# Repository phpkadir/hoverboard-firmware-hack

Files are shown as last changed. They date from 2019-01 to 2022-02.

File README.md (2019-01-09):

# Hoverboard-Firmware-Hack



### Under heavy development

This firmware is much better than the old one. tested up to 40A / 60V, no dead board so far :)
But The Firmware can't do inpossible Stuff pleace stay at 12s (under 50V) because the boards use condensators up to 50V higher voltages damage them.

This repo contains open source firmware for generic Hoverboard Mainboards.
The firmware you can find here allows you to use your Hoverboard Hardware (like the Mainboard, Motors and Battery) for cool projects like driving armchairs, person-tracking transportation robots and every other application you can imagine that requires controlling the Motors.

If you want an overview of what you can do with this firmware, here is a ~40min video of a talk about this project:
https://media.ccc.de/v/gpn18-95-howto-moving-objects

---

#### Hardware
otter

The original Hardware supports two 4-pin cables that originally were connected to the two sensor boards. They break out GND, 12/15V and USART2&3 of the Hoverboard mainboard.
Both USART2 & 3 can be used for UART and I2C, PA2&3 can be used as 12bit ADCs.

The reverse-engineered schematics of the mainboard can be found here:
http://vocke.tv/lib/exe/fetch.php?media=20150722_hoverboard_sch.pdf

---

#### Flashing
To build the firmware, just type "make". Make sure you have specified your gcc-arm-none-eabi binary location in the Makefile ("PREFIX = ..."). Right to the STM32, there is a debugging header with GND, 3V3, SWDIO and SWCLK. Connect GND, SWDIO and SWCLK to your SWD programmer, like the ST-Link found on many STM devboards.

Make sure you hold the powerbutton or connect a jumper to the power button pins while flashing the firmware, as the STM might release the power latch and switches itself off during flashing. Battery > 36V have to be connected while flashing.

To flash the STM32, use the ST-Flash utility (https://github.com/texane/stlink).

If you never flashed your mainboard before, the STM is probably locked. To unlock the flash, use the following OpenOCD command:

```
make unlock
```
if it fails use
```
make fallback_unlock
```
if it doest work now use *Windows utility*

Then you can simply flash the firmware:
```
make flash
```

---
#### Troubleshooting
First, check that power is connected and voltage is >36V while flashing.
If the board draws more than 100mA in idle, it's probably broken.

If the motors do something, but don't rotate smooth and quietly, try to use an alternative phase mapping. Usually, color-correct mapping (blue to blue, green to green, yellow to yellow) works fine. However, some hoverboards have a different layout then others, and this might be the reason your motor isn't spinning.

Nunchuck not working: Use the right one of the 2 types of nunchucks. Use i2c pullups.

Nunchuck or PPM working bad: The i2c bus and PPM signal are very sensitive to emv distortions of the motor controller. They get stronger the faster you are. Keep cables short, use shielded cable, use ferrits, stabalize voltage in nunchuck or reviever, add i2c pullups. To many errors leads to very high accelerations which triggers the protection board within the battery to shut everything down.

Most robust way for input is to use the ADC and potis. It works well even on 1m unshielded cable. Solder ~100k Ohm resistors between ADC-inputs and gnd directly on the mainboard. Use potis as pullups to 3.3V.

---

#### Examples

We want support many projects like a longboard. our firmware will support variable sync with i2c and an i2c display PPM-Sum signal and ADC input
It will get new fieldweakoning algorythm and a timing algorythm

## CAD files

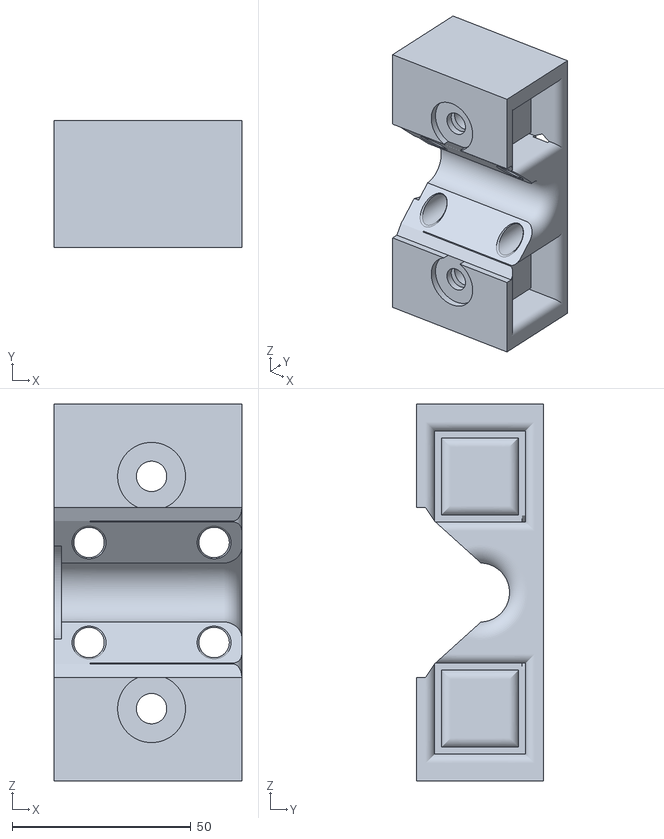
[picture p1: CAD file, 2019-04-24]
3d printable files/bobbycar/hinterachse1.stl
52.5 x 35.5 x 105.5

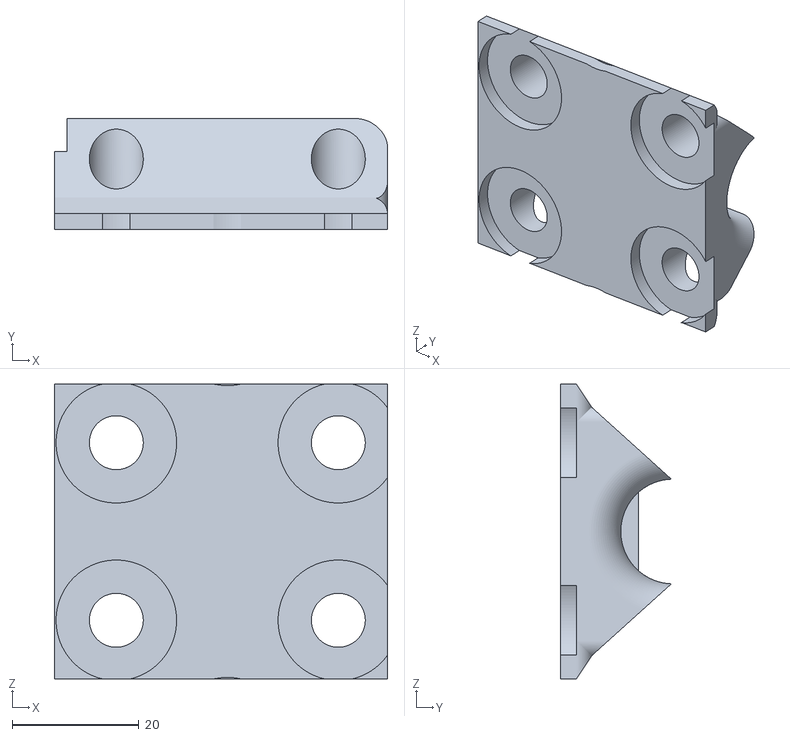
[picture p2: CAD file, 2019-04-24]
3d printable files/bobbycar/hinterachse2.stl
52.5 x 17.5 x 46.5

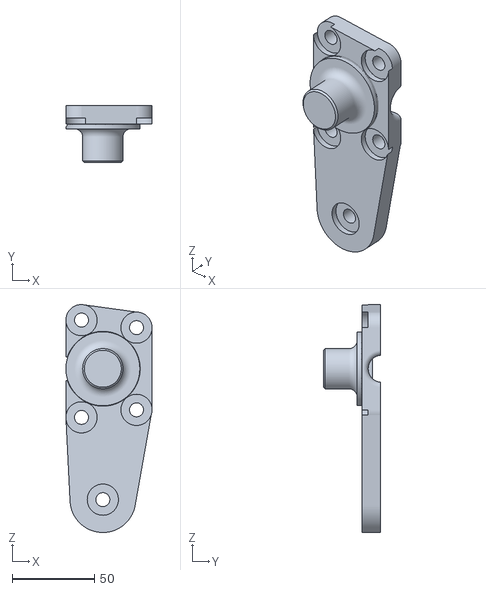
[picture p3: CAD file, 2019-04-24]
3d printable files/bobbycar/radaufnahme1 (1x normal, 1x gespiegelt).stl
52.5 x 34.8 x 138.8

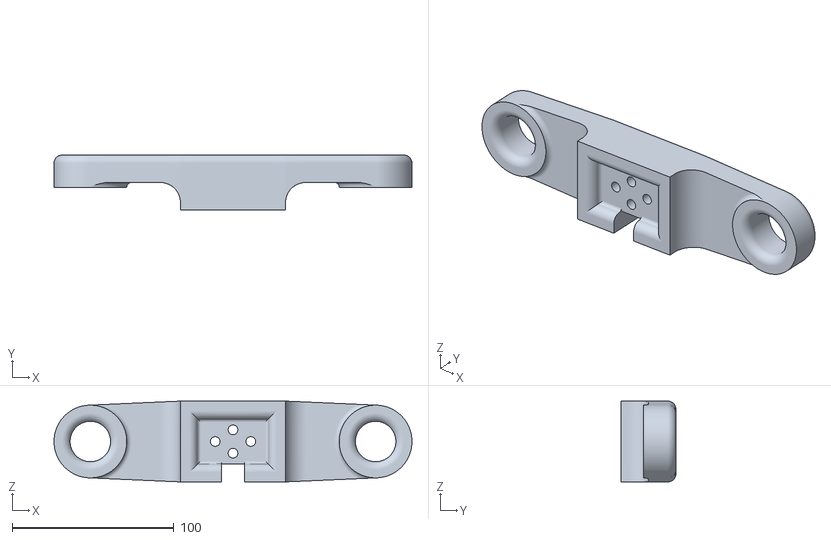
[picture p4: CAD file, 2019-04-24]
3d printable files/bobbycar/achsschenkel.stl
221.5 x 34.0 x 50.0

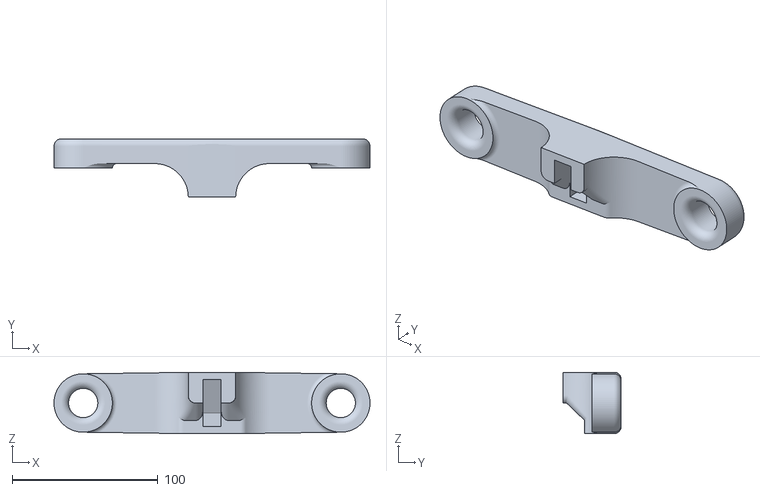
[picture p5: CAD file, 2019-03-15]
3d printable files/bobbycar/spurstange.stl
216.5 x 40.0 x 42.0

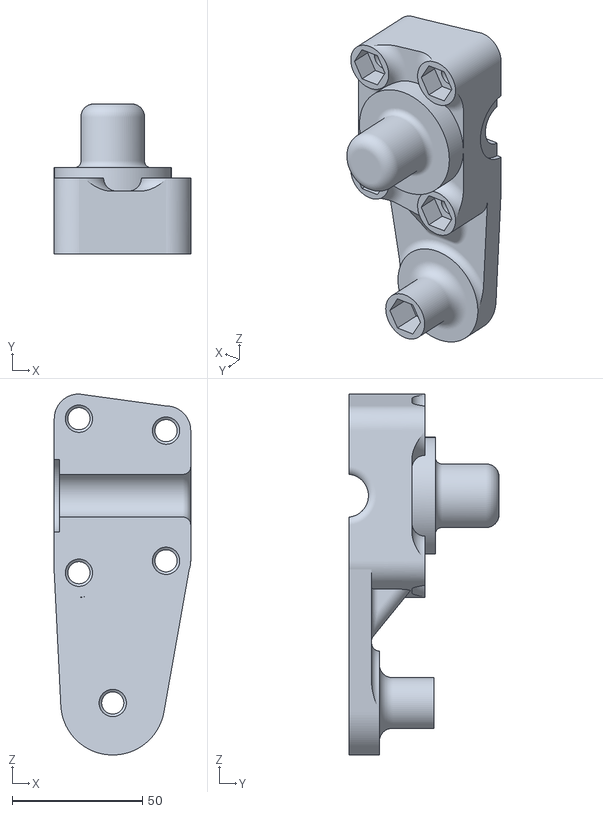
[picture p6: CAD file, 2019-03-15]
3d printable files/bobbycar/radaufnahme2 (1x normal, 1x gespiegelt).stl
52.5 x 57.8 x 138.8

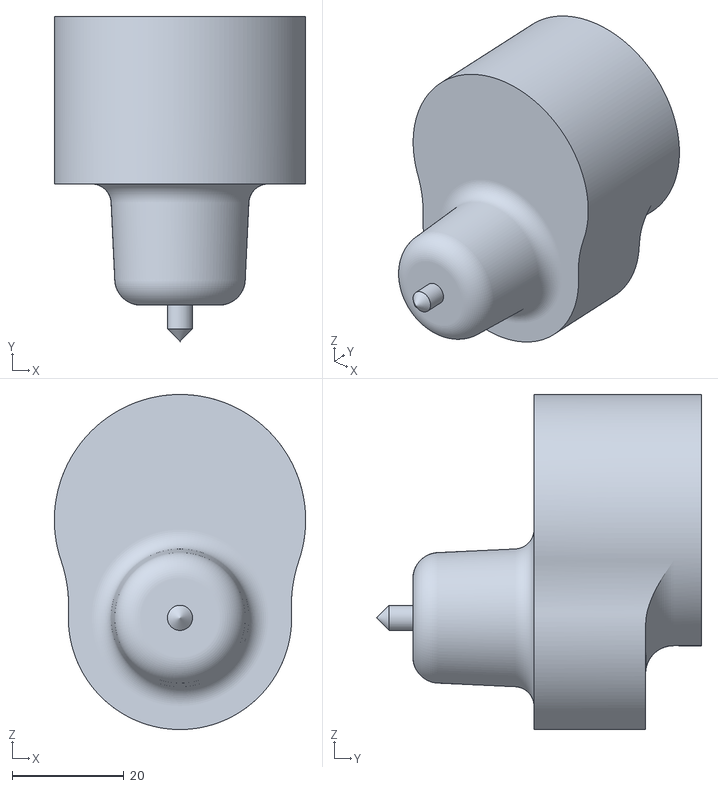
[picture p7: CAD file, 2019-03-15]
3d printable files/bobbycar/domlager (2x).stl
45.0 x 58.2 x 60.0

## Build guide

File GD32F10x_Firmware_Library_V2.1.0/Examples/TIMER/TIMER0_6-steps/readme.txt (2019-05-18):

/*!
    \file  readme.txt
    \brief description of the TIMER0 6-steps demo

    \version 2014-12-26, V1.0.0, firmware for GD32F10x
    \version 2017-06-20, V2.0.0, firmware for GD32F10x
    \version 2018-07-31, V2.1.0, firmware for GD32F10x
*/

/*
    Copyright (c) 2018, GigaDevice Semiconductor Inc.

    All rights reserved.

    Redistribution and use in source and binary forms, with or without modification, 
are permitted provided that the following conditions are met:

    1. Redistributions of source code must retain the above copyright notice, this 
       list of conditions and the following disclaimer.
    2. Redistributions in binary form must reproduce the above copyright notice, 
       this list of conditions and the following disclaimer in the documentation 
       and/or other materials provided with the distribution.
    3. Neither the name of the copyright holder nor the names of its contributors 
       may be used to endorse or promote products derived from this software without 
       specific prior written permission.

    THIS SOFTWARE IS PROVIDED BY THE COPYRIGHT HOLDERS AND CONTRIBUTORS "AS IS" 
AND ANY EXPRESS OR IMPLIED WARRANTIES, INCLUDING, BUT NOT LIMITED TO, THE IMPLIED 
WARRANTIES OF MERCHANTABILITY AND FITNESS FOR A PARTICULAR PURPOSE ARE DISCLAIMED. 
IN NO EVENT SHALL THE COPYRIGHT HOLDER OR CONTRIBUTORS BE LIABLE FOR ANY DIRECT, 
INDIRECT, INCIDENTAL, SPECIAL, EXEMPLARY, OR CONSEQUENTIAL DAMAGES (INCLUDING, BUT 
NOT LIMITED TO, PROCUREMENT OF SUBSTITUTE GOODS OR SERVICES; LOSS OF USE, DATA, OR 
PROFITS; OR BUSINESS INTERRUPTION) HOWEVER CAUSED AND ON ANY THEORY OF LIABILITY, 
WHETHER IN CONTRACT, STRICT LIABILITY, OR TORT (INCLUDING NEGLIGENCE OR OTHERWISE) 
ARISING IN ANY WAY OUT OF THE USE OF THIS SOFTWARE, EVEN IF ADVISED OF THE POSSIBILITY 
OF SUCH DAMAGE.
*/

  This demo is based on the GD32107C-EVAL board, it shows how to 
configure the TIMER0 peripheral to generate three complementary TIMER0 signals 
(for BLDC ) with dead time.

  TIMER0CLK is fixed to systemcoreclock, the TIMER0 prescaler is equal to 108 so the 
TIMER0 counter clock used is 1MHz.
  
  Channel change sequence: 
  AB`->AC`->BC`->BA`->CA`->CB`
step1:1-0  0-1  0-0   (CH0-CH0N  CH1-CH1N  CH2-CH2N)
step2:1-0  0-0  0-1   (CH0-CH0N  CH1-CH1N  CH2-CH2N)
step3:0-0  1-0  0-1   (CH0-CH0N  CH1-CH1N  CH2-CH2N)
step4:0-1  1-0  0-0   (CH0-CH0N  CH1-CH1N  CH2-CH2N)
step5:0-1  0-0  1-0   (CH0-CH0N  CH1-CH1N  CH2-CH2N)
step6:0-0  0-1  1-0   (CH0-CH0N  CH1-CH1N  CH2-CH2N)

  Connect the TIMER0 pins to a logic analyzer to monitor the different waveforms:
  - TIMER0_CH0  pin (PA8)
  - TIMER0_CH0N pin (PB13)
  - TIMER0_CH1  pin (PA9)
  - TIMER0_CH1N pin (PB14)
  - TIMER0_CH2  pin (PA10)
  - TIMER0_CH2N pin (PB15)

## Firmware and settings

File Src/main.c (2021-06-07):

/*
* This file is part of the hoverboard-firmware-hack project.
*
* Copyright (C) 2017-2018 Rene Hopf <renehopf@mac.com>
* Copyright (C) 2017-2018 Nico Stute <crinq@crinq.de>
* Copyright (C) 2017-2018 Niklas Fauth <niklas.fauth@kit.fail>
*
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
* You should have received a copy of the GNU General Public License
* along with this program.  If not, see <http://www.gnu.org/licenses/>.
*/

#include <stdbool.h>
#include <stdint.h>
#include "stm32f1xx_hal.h"  // main code for stm32 controller
#include "defines.h"  // for the macros
#include "setup.h"  // for access the functions form setup
#include "bldc.h"  // for the main control variables
#include "buzzertones.h"
#include "hd44780.h"  // for the display
#include "config.h"  // the config
#include "comms.h"
#include "control.h"
#include "generic_device.h"
void SystemClock_Config(void);

void init(){
    HAL_Init();
    __HAL_RCC_AFIO_CLK_ENABLE();
    HAL_NVIC_SetPriorityGrouping(NVIC_PRIORITYGROUP_4);
    /* System interrupt init*/
    /* MemoryManagement_IRQn interrupt configuration */
    HAL_NVIC_SetPriority(MemoryManagement_IRQn, 0, 0);
    /* BusFault_IRQn interrupt configuration */
    HAL_NVIC_SetPriority(BusFault_IRQn, 0, 0);
    /* UsageFault_IRQn interrupt configuration */
    HAL_NVIC_SetPriority(UsageFault_IRQn, 0, 0);
    /* SVCall_IRQn interrupt configuration */
    HAL_NVIC_SetPriority(SVCall_IRQn, 0, 0);
    /* DebugMonitor_IRQn interrupt configuration */
    HAL_NVIC_SetPriority(DebugMonitor_IRQn, 0, 0);
    /* PendSV_IRQn interrupt configuration */
    HAL_NVIC_SetPriority(PendSV_IRQn, 0, 0);
    /* SysTick_IRQn interrupt configuration */
    HAL_NVIC_SetPriority(SysTick_IRQn, 0, 0);

    SystemClock_Config();

    __HAL_RCC_DMA1_CLK_DISABLE();
    MX_GPIO_Init();
    MX_TIM_Init();
    MX_ADC1_Init();
    MX_ADC2_Init();

    HAL_GPIO_WritePin(OFF_PORT, OFF_PIN, 1);  // set latch to on

    HAL_ADC_Start(&hadc1);
    HAL_ADC_Start(&hadc2);

    set_buzzer(startUpSound);

    HAL_GPIO_WritePin(LED_PORT, LED_PIN, 1);  // turn LED on for looking if the µC is working

    #ifdef CONTROL_PPM
      PPM_Init();
    #endif

      I2C_Init();
      HAL_Delay(50);

    load_eeprom();  // initialize variables from eeprom or initialize them
    while(HAL_GPIO_ReadPin(BUTTON_PORT, BUTTON_PIN));  // wait for button release
}

int main(void) {
restart = true;
main_start:  // only for defect boards if you think your hardware is working please remove
  init();
  device_init();
  set_bldc_motors(true);
  while(1) {
    HAL_Delay(3);
    device_specific();
    //START FINAL CODE
    if (HAL_GPIO_ReadPin(BUTTON_PORT, BUTTON_PIN)) {  // turnoff mechanism
      bool btn_release = false;
      unsigned long startTime = get_mainCounter();
      set_bldc_motors(false);
      while(get_mainCounter() < (startTime + (PWM_FREQ * 2))){  // check button for 2s for release to only turn off if its pressed for 2 secs
        if(!HAL_GPIO_ReadPin(BUTTON_PORT, BUTTON_PIN)){  // if button released
          btn_release = true;
          break;
        }
      }
      if(btn_release){
        set_buzzer(buttonRelease);
        set_bldc_motors(true);
        // do something
        device_button();
      }
      else{
        set_buzzer(shutDownSound);
        while (get_mainCounter() < (startTime + (PWM_FREQ * 10))) {
          if(!HAL_GPIO_ReadPin(BUTTON_PORT, BUTTON_PIN)){
            btn_release = true;
            break;
          }
        }  // wait for button release to turn off
        if(btn_release) {
          turnOff();
          break;
        } else {
          set_buzzer(resetSound);
          while(HAL_GPIO_ReadPin(BUTTON_PORT, BUTTON_PIN));
          turnOffWithReset();
          break;
        }
      }
    }
    //END FINAL CODE
    if(BATTERY_VOLTAGE2ADC12(DEBUG_VOLTAGE_LOW) < battery_voltage && battery_voltage < BATTERY_VOLTAGE2ADC12(DEBUG_VOLTAGE_HIGH)){
      // Debug mode
    }    
    else if (battery_voltage < lowBattery[0]) {
      set_buzzer(lowBatTones[0]);
      set_bldc_motors(false);
      HAL_Delay(200);
      turnOff();
      break;
    }
    for(uint8_t x=1;x<lowBattery_length;x++)
      if  (battery_voltage < lowBattery[x]) {
        set_buzzer(lowBatTones[x]);
        LIMIT_CURRENT(5 + 5*x);  // limiting the motorcurrent to a lower value
        break;
      }
  }
  goto main_start;  // if this goto is used the board is defect and everybody knows: "Defect boards are liking defect code" :D
}

/** System Clock Configuration
*/
void SystemClock_Config(void) {
  RCC_OscInitTypeDef RCC_OscInitStruct;
  RCC_ClkInitTypeDef RCC_ClkInitStruct;
  RCC_PeriphCLKInitTypeDef PeriphClkInit;

  /**Initializes the CPU, AHB and APB busses clocks
    */
  RCC_OscInitStruct.OscillatorType      = RCC_OSCILLATORTYPE_HSI;
  RCC_OscInitStruct.HSIState            = RCC_HSI_ON;
  RCC_OscInitStruct.HSICalibrationValue = 16;
  RCC_OscInitStruct.PLL.PLLState        = RCC_PLL_ON;
  RCC_OscInitStruct.PLL.PLLSource       = RCC_PLLSOURCE_HSI_DIV2;
  RCC_OscInitStruct.PLL.PLLMUL          = RCC_PLL_MUL16;
  HAL_RCC_OscConfig(&RCC_OscInitStruct);

  /**Initializes the CPU, AHB and APB busses clocks
    */
  RCC_ClkInitStruct.ClockType      = RCC_CLOCKTYPE_HCLK | RCC_CLOCKTYPE_SYSCLK | RCC_CLOCKTYPE_PCLK1 | RCC_CLOCKTYPE_PCLK2;
  RCC_ClkInitStruct.SYSCLKSource   = RCC_SYSCLKSOURCE_PLLCLK;
  RCC_ClkInitStruct.AHBCLKDivider  = RCC_SYSCLK_DIV1;
  RCC_ClkInitStruct.APB1CLKDivider = RCC_HCLK_DIV2;
  RCC_ClkInitStruct.APB2CLKDivider = RCC_HCLK_DIV1;

  HAL_RCC_ClockConfig(&RCC_ClkInitStruct, FLASH_LATENCY_2);

  PeriphClkInit.PeriphClockSelection = RCC_PERIPHCLK_ADC;
  PeriphClkInit.AdcClockSelection    = RCC_ADCPCLK2_DIV8;
  HAL_RCCEx_PeriphCLKConfig(&PeriphClkInit);

  /**Configure the Systick interrupt time
    */
  HAL_SYSTICK_Config(HAL_RCC_GetHCLKFreq() / 1000);

  /**Configure the Systick
    */
  HAL_SYSTICK_CLKSourceConfig(SYSTICK_CLKSOURCE_HCLK);

  /* SysTick_IRQn interrupt configuration */
  HAL_NVIC_SetPriority(SysTick_IRQn, 0, 0);
}

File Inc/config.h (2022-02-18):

#pragma once
#include "stm32f1xx_hal.h"

// ################################################################################

#define PWM_FREQ         16000      // PWM frequency in Hz default 16k  // h bridge pwm frequency: OC -> lovering deadtime!
#define DEAD_TIME        32         // PWM deadtime        default 32 0.5µS   // h bridge calibration for mosfet burning them OC possible
#define BAT_CALIB_REAL_VOLTAGE        43.0       // input voltage measured by multimeter
#define BAT_CALIB_ADC                 1704       // adc-value measured by mainboard (value nr 5 on UART debug output)

//device specific
#define DEAD_ZONE 64
#define BAT_CELL_CNT     10.0
#define BAT_FULL_CELL    4.2
#define BAT_RATED_CELL   3.6
#define BAT_LOW1_CELL    3.4
#define BAT_LOW2_CELL    3.2
#define BAT_LOW_DEAD_CELL 3.0
#define DEBUG_VOLTAGE_LOW 33.5
#define DEBUG_VOLTAGE_HIGH 36.5
#define THROTTLE_REVERSE_MAX (-(THROTTLE_MAX * 3 / 10))
//#define THROTTLE_REVERSE_MAX (-THROTTLE_MAX)
#define BEEPS_BACKWARD

#define I2C_MASTER
// ################################################################################

//#define DEBUG_SERIAL_USART3         // left sensor board cable, disable if ADC or PPM is used!
//#define DEBUG_SERIAL_USART3         // right sensor board cable, disable if I2C (nunchuck) is used!
//#define DEBUG_BAUD       115200     // UART baud rate
//#define DEBUG_SERIAL_SERVOTERM
//#define DEBUG_SERIAL_ASCII          // human readable output. i.e. "345;1337;0;0\n\r"

//#define CONTROL_SERIAL_USART2
//#define CONTROL_BAUD       19200     // control via usart from eg an Arduino or raspberry
// for Arduino, use void loop(void){ Serial.write((uint8_t *) &steer, sizeof(steer)); Serial.write((uint8_t *) &speed, sizeof(speed));delay(20); }

//#define DEBUG_I2C_LCD               // standard 16x2 or larger text-lcd via i2c-converter on right sensor board cable

#define TIMEOUT          5          // number of wrong / missing commands before emergency off

// ################################################################################

// ###### CONTROL VIA RC REMOTE ######
// left sensor board cable. Channel 1: steering, Channel 2: speed.
#define PPM_NUM_CHANNELS 6          // total number of PPM channels to receive, even if they are not used.

// ###### CONTROL VIA TWO POTENTIOMETERS ######
// ADC-calibration to cover the full poti-range: connect potis to left sensor board cable (0 to 3.3V), watch UART on the right sensor board cable. the first 2 values are ADC1 and ADC2. write minimum and maximum poti position-values to ADC?_MIN and ADC?_MAX.
#define CONTROL_ADC                 // use ADC as input. disable DEBUG_SERIAL_USART2!
#define ADC_MIN 0                  // min ADC1-value while poti at minimum-position (0 - 4095)
#define ADC_MAX 4095               // max ADC1-value while poti at maximum-position (0 - 4095)
#define ADC_MID 2048

// ###### CONTROL VIA NINTENDO NUNCHUCK ######
// left sensor board cable. keep cable short, use shielded cable, use ferrits, stabalize voltage in nunchuck, use the right one of the 2 types of nunchucks, add i2c pullups.
//#define CONTROL_NUNCHUCK            // use nunchuck as input. disable DEBUG_SERIAL_USART3!

// ################################################################################

// ###### DRIVING BEHAVIOR ######

#define INVERT_L_DIRECTION
#if !defined(INVERT_L_DIRECTION)
#define INVERT_R_DIRECTION
#endif // INVERT_R_DIRECTION

#define  PWM_MIN 0
#define PWM_MAX (PWM_RES / 2)
#define WEAKING_PWM_MAX (PWM_MAX*45/100)
#define THROTTLE_MAX 1000
#define PERIOD6KMH (PWM_FREQ / 50)
// ################################################################################

// validate settings (do not touch this):

#if defined DEBUG_SERIAL_USART2 && defined CONTROL_ADC
  #error CONTROL_ADC and DEBUG_SERIAL_USART2 not allowed. use DEBUG_SERIAL_USART3 instead.
#endif

#if defined DEBUG_SERIAL_USART2 && defined CONTROL_PPM
  #error CONTROL_PPM and DEBUG_SERIAL_USART2 not allowed. use DEBUG_SERIAL_USART3 instead.
#endif

#if defined DEBUG_SERIAL_USART3 && defined CONTROL_NUNCHUCK
  #error CONTROL_NUNCHUCK and DEBUG_SERIAL_USART3 not allowed. use DEBUG_SERIAL_USART2 instead.
#endif

#if defined CONTROL_PPM && defined CONTROL_ADC && defined CONTROL_NUNCHUCK || defined CONTROL_PPM && defined CONTROL_ADC || defined CONTROL_ADC && defined CONTROL_NUNCHUCK || defined CONTROL_PPM && defined CONTROL_NUNCHUCK
  #error only 1 input method allowed. use CONTROL_PPM or CONTROL_ADC or CONTROL_NUNCHUCK.
#endif

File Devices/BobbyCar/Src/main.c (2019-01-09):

#include "bobbycar.h"
void device_specific(){
    int tmp_trottle[2];
    calc_torque_per_wheel(
      calc_torque(
        clean_adc(virtual_ival[0][0]),
        clean_adc(virtual_ival[0][1])),
      calc_steering_eagle(clean_adc(virtual_ival[1][0])),
      tmp_trottle);
    #ifdef BEEPS_BACKWARD
    if(tmp_trottle[0] + tmp_trottle[1] < 0){
      set_buzzer(reverseSound);
    }
    #endif
    set_throttle(tmp_trottle[0], tmp_trottle[1]);
}

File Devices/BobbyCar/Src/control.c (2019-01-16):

#include "bobbycar.h"

int clean_adc(uint32_t inval){
  if((inval << 16)-DEAD_ZONE-ADC_MIN<0)
    return PWM_MIN;  // if ival in under deadzone
	else if((inval << 16)>ADC_MAX-2*DEAD_ZONE)
    return PWM_MAX;  // if ival in upper deadzone
  else
	  return (((inval << 16) - DEAD_ZONE - ADC_MIN) * (PWM_MAX - PWM_MIN)) / (ADC_MAX - ADC_MIN) + PWM_MIN;  // Map value linear to area in PWM area
}

int calc_torque(int throttle,int breaks){
  if(breaks == 0){  // drive forward
    return throttle;
}
  else if(breaks == PWM_MAX){  // drive backwards
    return -throttle;
  }
  else{
    return throttle-breaks;
  }
}
#define STEERING_EAGLE_FACTOR 0.01
float calc_steering_eagle(int inval){
  return (float)inval * STEERING_EAGLE_FACTOR;
}

inline void calc_torque_per_wheel(int throttle, float steering_eagle, int* torque){
  int back_wheel = WHEELBASE / tan(abs(steering_eagle));
  int radius_main = sqrt(pow(back_wheel, 2)+pow(WHEELBASE / 2 ,2));
#if !defined(STEERING)
  torque[0] = (back_wheel + WHEEL_WIDTH/2 * SIGN(steering_eagle)) * throttle / radius_main;
  torque[1] = (back_wheel - WHEEL_WIDTH/2 * SIGN(steering_eagle)) * throttle / radius_main;
#else
  #define wheel_bl (back_wheel + (WHEEL_WIDTH/2 * SIGN(steering_eagle) - STEERING_TO_WHEEL_DIST))
  #define wheel_br (back_wheel - (WHEEL_WIDTH/2 * SIGN(steering_eagle) - STEERING_TO_WHEEL_DIST))
  torque[0] = (sqrt(pow(wheel_bl, 2)+pow(WHEELBASE,2)) + STEERING_TO_WHEEL_DIST * SIGN(steering_eagle)) * throttle / radius_main;
  torque[1] = (sqrt(pow(wheel_br, 2)+pow(WHEELBASE,2)) - STEERING_TO_WHEEL_DIST * SIGN(steering_eagle)) * throttle / radius_main;
  #undef wheel_bl
  #undef wheel_br
#endif
}



/*int clean_adc(uint32_t inval){
  if((inval << 16)-DEAD_ZONE-ADC_MIN<0)
    return PWM_MIN;  // if ival in under deadzone
	else if((inval << 16)>ADC_MAX-2*DEAD_ZONE)
    return PWM_MAX;  // if ival in upper deadzone
  else
	  return (((inval << 16) - DEAD_ZONE - ADC_MIN) * (PWM_MAX - PWM_MIN)) / (ADC_MAX - ADC_MIN) + PWM_MIN;  // Map value linear to area in PWM area
}

#define WHEELBASE 2
#define WHEEL_WIDTH 1
#define STEERING_TO_WHEEL_DIST 1

inline void calc_torque_per_wheel(int throttle, float steering_eagle, int* torque){
  int back_wheel = WHEELBASE / tan(abs(steering_eagle));
  int radius_main = sqrt(pow(back_wheel, 2)+pow(WHEELBASE / 2 ,2));
#if !defined(STEERING)
  torque[0] = (back_wheel + WHEEL_WIDTH/2 * SIGN(steering_eagle)) * throttle / radius_main;
  torque[1] = (back_wheel - WHEEL_WIDTH/2 * SIGN(steering_eagle)) * throttle / radius_main;
#else
  #define wheel_bl (back_wheel + (WHEEL_WIDTH/2 * sign(steering_eagle) - STEERING_TO_WHEEL_DIST))
  #define wheel_br (back_wheel - (WHEEL_WIDTH/2 * sign(steering_eagle) - STEERING_TO_WHEEL_DIST))
  torque[0] = (sqrt(pow(wheel_bl, 2)+pow(WHEELBASE,2)) + STEERING_TO_WHEEL_DIST * sign(steering_eagle)) * throttle / radius_main;
  torque[1] = (sqrt(pow(wheel_br, 2)+pow(WHEELBASE,2)) - STEERING_TO_WHEEL_DIST * sign(steering_eagle)) * throttle / radius_main;
  #undef wheel_bl
  #undef wheel_br
#endif
}

int calc_torque(int throttle,int breaks){
  if(breaks == 0){  // drive forward
    return throttle;
}
  else if(breaks == PWM_MAX){  // drive backwards
    return -throttle;
  }
  else{
    return throttle-breaks;
  }
}
#define STEERING_EAGLE_FACTOR 0.01
float calc_steering_eagle(int inval){
  return (float)inval * STEERING_EAGLE_FACTOR;
}
*/

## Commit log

2018-07-11 bldc cleanups
2018-07-11 bldc linear fealdweakening added
2018-07-11 freql and freqr implementet: I hope its a timer interrupt
2018-10-29 Update Src/bldc.c
    updating bldc code...
2018-10-29 Update Src/bldc.c
    inc initvals to 2048 added a few vals
2018-11-05 some bldc changes
2018-11-05 opt bldc
2018-11-05 variable current limit limit the no limitmode to 60 amps (max of mosfet)
2018-11-05 shorter name because it'll get a 16x2 LED
    [weaking.c]
2018-11-13 array for adc
2018-11-14 Current motor cutoff looped
2018-11-14 few errors
    Src/comms.c:15:31: note: (near initialization for 'virutal_phase[0]')
    Src/comms.c:19:41: error: initializer element is not constant
    const int *virtual_ival[] = {_buff_ival,(int*)&(adc_array[2])};
    [bldc.c, comms.c, control.c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]
2018-11-23 added comments and stated to implement sensorless currentdriven bldc control
2018-11-24 added comments and fixed simple bugs
    [bldc.c]
2018-11-28 torque per wheel...
2018-11-28 finished torque per wheel *untested*
2018-11-28 bldc fix
2018-11-28 added clamp in BLDC set throtte
2018-11-29 added parts for i2c master slave init
2018-11-29 Added algorythm to calculate wheels
2018-12-01 added vars for timing to boost the motorspeed a bit more
2018-12-16 fixed a direction bug internal with adding a new var
    [bldc.c]
2019-01-01 Need some errorfixing but better codebase!! NOT BUILDABLE
    [bldc.c, buzzertones.c, main.c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]
2019-01-01 a bit codebase rework
    [bldc.c, buzzertones.c, main.c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]
2019-01-01 disable output (disable motors and buzzer)
    [bldc.c]
2019-01-01 added new mem area for saving vars (fast init and battery calibration)
2019-01-01 bldc: buzzer for batterysound rdy && inplemented sounds
    [bldc.c, buzzertones.c]
2019-01-05 bldc fauth code
2019-01-05 tests going on motors working with software of fauth but not mine
2019-01-05 finaly works :) :) better BLDC code
2019-01-05 added CLAMP
2019-01-05 battery voltage as adc<<10 value
2019-01-07 prepairing multiple devices
2019-01-07 added fallback turnoff of boards with defect latch curcit
2019-01-09 fixed a few warnings
    [bldc.c, buzzertones.c, control.c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]
2019-01-09 added button to generic device
2019-01-14 moved code to generic device file
2019-01-27 fixed deadboard init and overclock
    [config.h, generic_device.c]
2019-02-04 enabled full throttle
2019-02-05 24 deadtime and 24k pwm makes problem shitty motorcontrol at higher rpm
    [config.h]
2019-02-10 restart bool to detect an hw reset
    [control.c, main.c]
2019-03-15 added printfiles 10*m8x40 sechkant (13er kopf) mit mutter benötigt
    [achsschenkel.stl, domlager (2x).stl, radaufnahme1 (1x normal, 1x gespiegelt).stl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]
2019-04-24 updatet stl files
    [achsschenkel.stl, hinterachse1.stl, hinterachse2.stl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]
2019-12-20 adding fixed rpm brushless control
    easydrive v1.0
    [comms.c, weaking.c]
2020-07-04 expo fixed reverse included
    [generic_device.c]
2020-07-27 adc buffer
2020-12-19 added code to eeprom manager and hoped for fix the nasty speed error
    [config.h, generic_device.c]
2020-12-21 added i2c
2020-12-22 added steering torque vectoring
2020-12-23 implementing torque vectoring
2022-03-10 underclock i2c

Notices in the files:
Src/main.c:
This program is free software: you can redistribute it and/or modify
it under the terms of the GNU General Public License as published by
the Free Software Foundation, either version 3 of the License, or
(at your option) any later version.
